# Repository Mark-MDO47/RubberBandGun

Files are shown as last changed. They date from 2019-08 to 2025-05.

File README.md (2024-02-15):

# RubberBandGun
A high-tech SciFi imagining of the rubber band gun.

Both working prototypes were shown at the Asheville Maker Faire on May 07, 2022 in Asheville, N.C. Estimates are that 100 people fired rubber bands out of the RBG!<br>
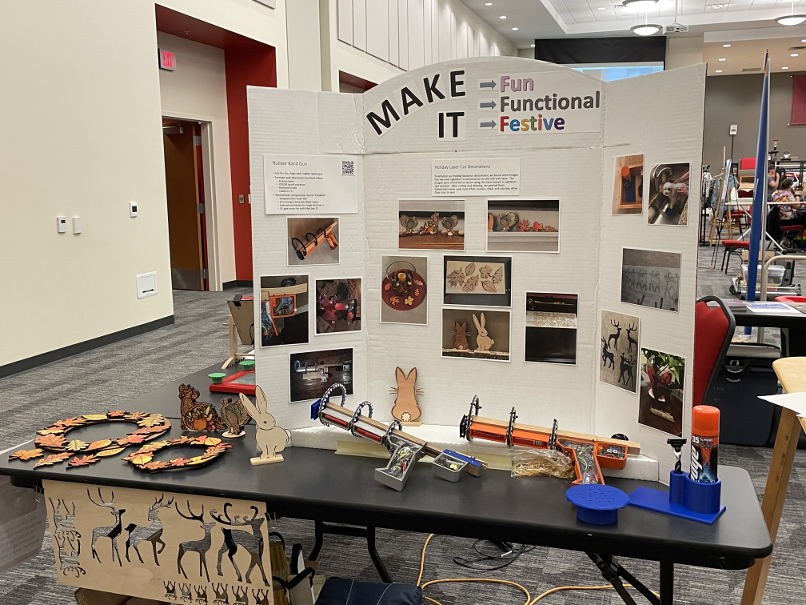
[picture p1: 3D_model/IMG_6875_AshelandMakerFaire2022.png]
Both Rubber Band Guns at Asheville Maker Faire on May 2022


**Table Of Contents**
* [Top](#rubberbandgun "Top")
* [Videos](#videos "Videos")
* [Images](#images "Images")
* [Introduction](#introduction "Introduction")
* [Parts List](#parts-list "Parts List")
  * [Release Mechanism Software Dependency](#release-mechanism-software-dependency "Release Mechanism Software Dependency")
* [Sounds](#sounds "Sounds")
  * [Sound Effects](#sound-effects "Sound Effects")
  * [Voice Audio](#voice-audio "Voice Audio")
* [LED Patterns](#led-patterns "LED Patterns")
* [Extras](#extras "Extras")
* [Guide to README and Other Docs](#guide-to-readme-and-other-docs "Guide to README and Other Docs")

## Videos
[Top](#rubberbandgun "Top")<br>
Here is a new (2023-07-14) video showing the completed orange "Sidewinder" rubber band gun with a fairly complete showing of its features.
* https://youtu.be/TYfbrVR2EE8

Here is a video showing the completed orange "Sidewinder" rubber band gun at night:
* https://youtu.be/M4FHvP624Kg

Here is a 2020-09-25 video demonstrating most of the software running on a prototype:
* https://youtu.be/njpYX-5Zv9Y

## Images
[Top](#rubberbandgun "Top")<br>

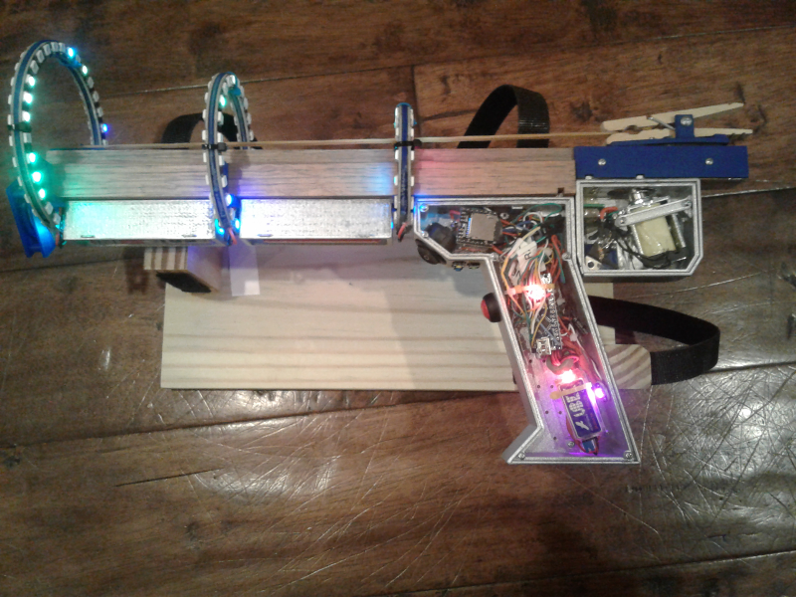
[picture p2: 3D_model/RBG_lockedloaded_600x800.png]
Top View of Jim's assembled SINGLETON SILVER RBG with solenoid and sliding barrel

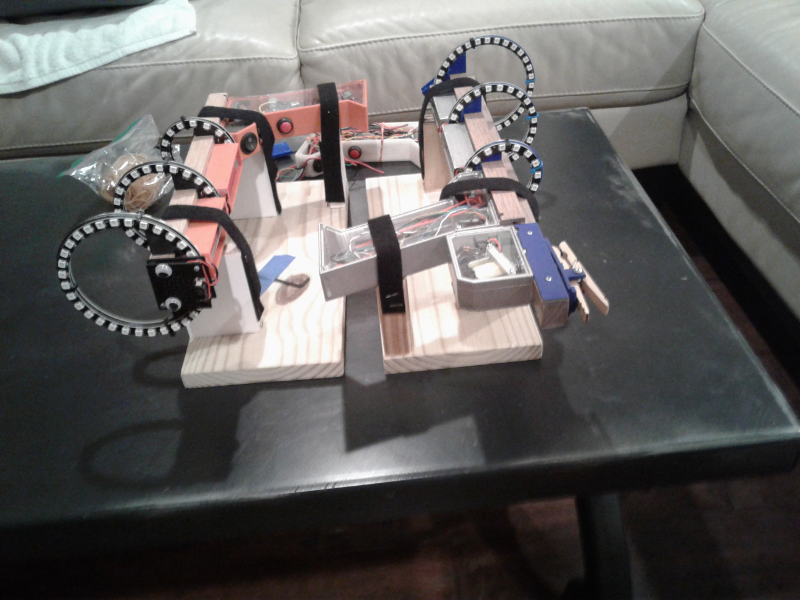
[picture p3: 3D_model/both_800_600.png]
Both RBGs side by side

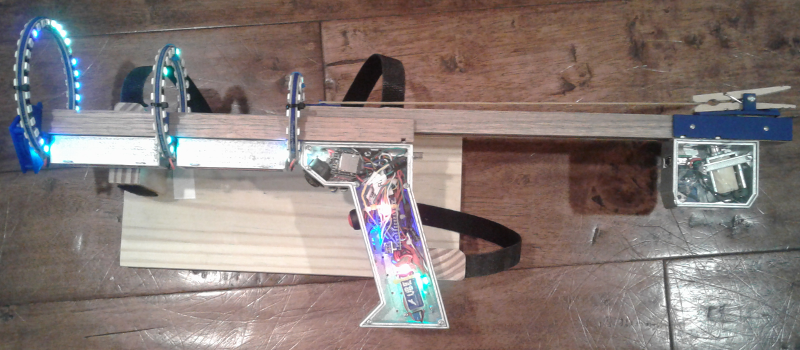
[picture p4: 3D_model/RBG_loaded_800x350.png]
Loading a rubber band in Jim's assembled SINGLETON SILVER RBG with solenoid and sliding barrel

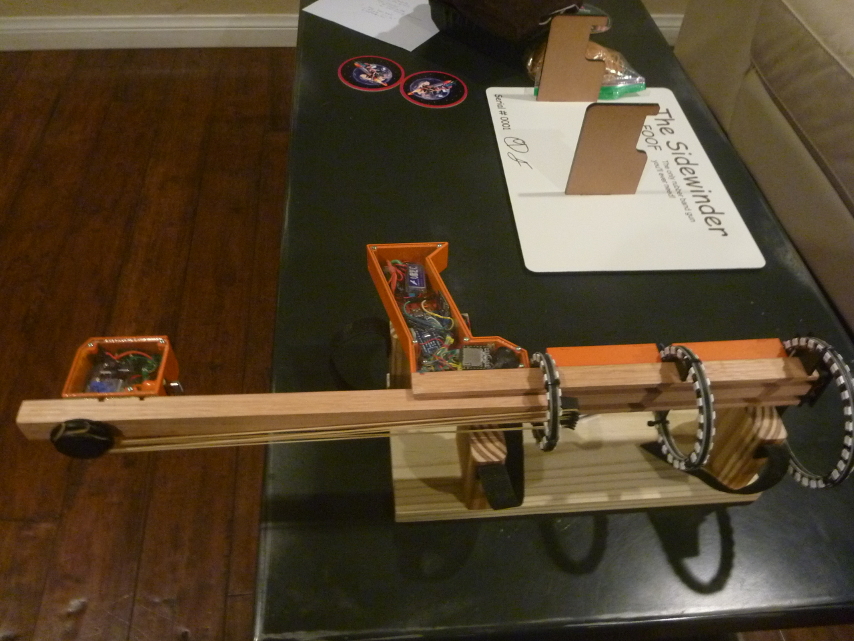
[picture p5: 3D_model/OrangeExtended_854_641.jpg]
Extended view of ORANGE SIDEWINDER Science Fiction Rubber Band Gun with Motor attachment

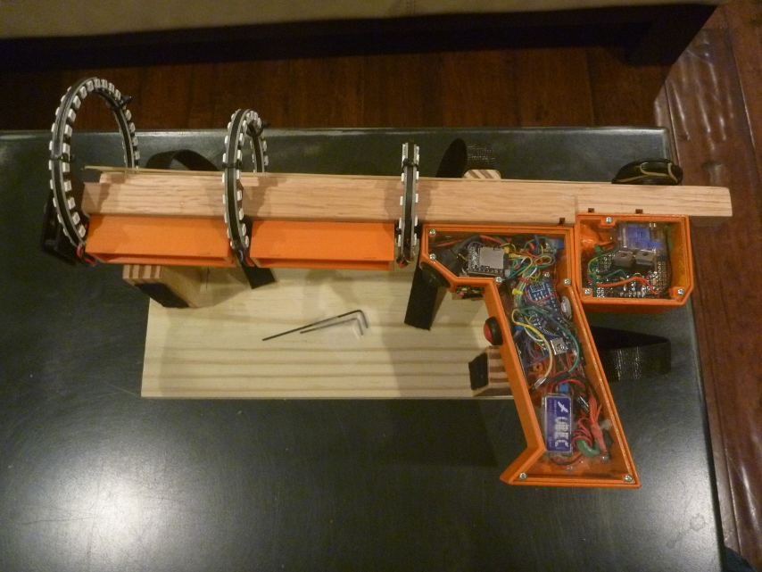
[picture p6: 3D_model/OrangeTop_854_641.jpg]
Top view of ORANGE SIDEWINDER Science Fiction Rubber Band Gun with Motor attachment

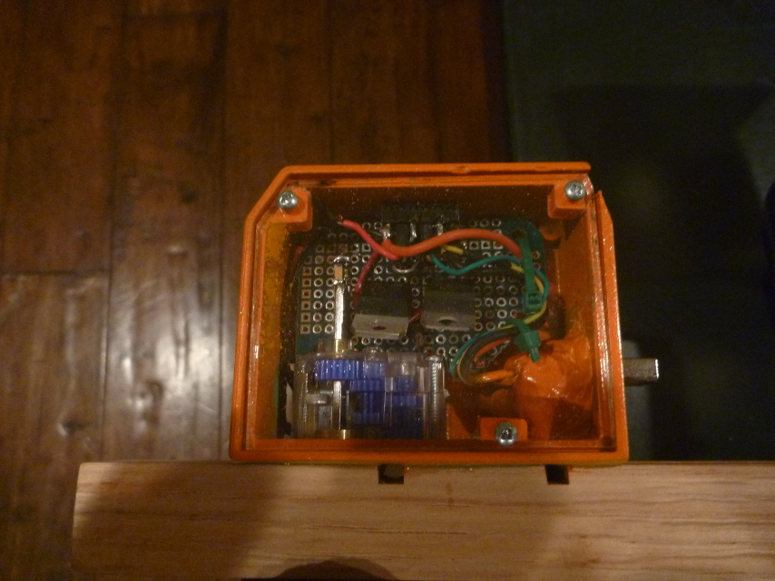
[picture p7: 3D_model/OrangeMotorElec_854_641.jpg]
View of ORANGE SIDEWINDER Science Fiction Rubber Band Gun Motor electronics

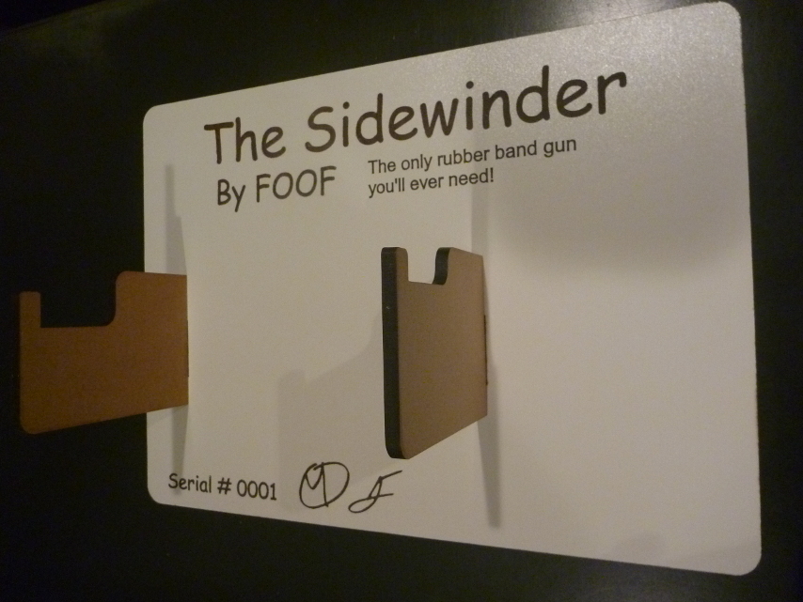
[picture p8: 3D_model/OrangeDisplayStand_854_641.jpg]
View of Display Stand for ORANGE SIDEWINDER Science Fiction Rubber Band Gun


## Introduction
[Top](#rubberbandgun "Top")<br>
Jim and I made a Science-Fiction Rubber Band Gun!

It has three rings of WS2812b 5050 RGB LED Ring proceeding up the barrel, each one larger than the previous in a "blunderbuss" shape. Note: this shape when applied to a handgun was known as a dragon, from which the term dragoon; see https://en.m.wikipedia.org/wiki/Blunderbuss

When fired, it plays a chosen sound. This could be a sequence similar to a "soundified" rendition of two neutron stars colliding
* https://www.gw-openscience.org/audiogwtc1 - search for GW170817

See the [Sounds](#sounds "Sounds") section below and the sounds README for more info.
* https://github.com/Mark-MDO47/RubberBandGun/blob/master/sounds/README.md

At the same time as the sound, the LED rings do patterns to make it look like they are being charged up followed by a sequential pulsing that would convince anyone who knows absolutely less than nothing about such things that a rail-gun effect is propelling the rubber band down the central tube. These rings are composed of WS2812B individually addressable color LEDs controlled by the fantastic FastLED library. See the [LED Patterns](#led-patterns "LED Patterns") section below and the PartsInfo README for more info.
* https://github.com/Mark-MDO47/RubberBandGun/blob/master/PartsInfo/README.md

And the RBG is a talking Rubber Band Gun! It can use its own built-in speaker or connect to a Bluetooth speaker, it has voice menus to allow configuration of sounds and LED effects. The video at https://youtu.be/njpYX-5Zv9Y goes through some of the menus using a Bluetooth speaker.

## Parts List
[Top](#rubberbandgun "Top")<br>
We have two working prototypes using these parts. The prices and parts availability have not been updated recently.
* https://github.com/Mark-MDO47/RubberBandGun/blob/master/PartsList.md

The barrel of the Rubber Band Gun is made from wood, with a sliding barrel attachment to assist in stringing the rubber band through the LED rings. The rest including the handgrip is 3-D printed.

### Release Mechanism Software Dependency
[Top](#rubberbandgun "Top")<br>
The "SILVER" SINGLETON RBG uses the solenoid release mechanism through the CLOTHESPIN to fire the rubber band.

Jim felt like this wasn't reliable enough and designed a SIDEWINDER mechanism that uses a motor to release one or more rubber bands at a time; this was used on the "ORANGE" RBG.

The current parts list and schematics contain both the CLOTHESPIN (SOLENOID) and the SIDEWINDER (MOTOR) mechanisms.

Git tag Silver-1.0 is the version of software that is in the SILVER CLOTHESPIN (SOLENOID) RBG
* There is a definition of DLYSOLENOID in RBG_SciFi_StatesAndInputs.h that needs to be adjusted if using the SIDEWINDER (MOTOR). See the comments near that definition if interested.

Development is continuing to make a minimum as well as a maximum activation time for the solenoid or motor mechanism. This will get a tag when complete and tested. SOLENOID_IF_NONZERO chooses CLOTHESPIN versus SIDEWINDER operation and sets the values of DLYSOLENOID_MIN and DLYSOLENOID_MAX.
* Define SOLENOID_IF_NONZERO as 1 for CLOTHESPIN (SOLENOID) processing.
  * The Silver-1.0 version DLYSOLENOID corresponds to DLYSOLENOID_MAX in the later versions.
* Define SOLENOID_IF_NONZERO as 0 for SIDEWINDER (MOTOR) processing; this also activates the ability to control the motor time with the trigger button between DLYSOLENOID_MIN and DLYSOLENOID_MAX. I had initially added some other factors like when the shooting sound ended, but opted for more predictable behavior.
  *  When it shoots, it will do a minimum of 1/4 turn and basically keep turning until you let the trigger off or it reaches 1 complete turn. This allows me to put a rubber band on every other notch and just get a single shot by momentary trigger press or multiple shots by holding the trigger down until done.

## Sounds
[Top](#rubberbandgun "Top")<br>
All sounds for the RBG were processed by Audacity, which can be found at https://www.audacityteam.org/

Voice sounds were generated by the eSpeak text-to-speech program version 1.48.04. The original code can be found at http://espeak.sourceforge.net/ while current development is at https://github.com/espeak-ng/espeak-ng
* Postprocessing was done by Audacity

The sounds reside on a 16Gbyte SD card inserted in the YX5200 audio module. Also on that SD card is an ATTRIBUTION directory containing an HTML file with attributions for the sounds used in this project.

Note that the sounds were de-stereo'd, chopped up, and in many cases modified and/or combined with other sounds. There is not a one-to-one onto relationship between the source of the sounds and the sounds as played by the Rubber Band Gun.

* As for many aspects of the RGB, the text-to-speech is semi-automated with StateTable_minimal.xlsx used to control generation and to associate sounds with RBG events.
* See https://github.com/Mark-MDO47/RubberBandGun/blob/master/sounds/README.md

### Sound Effects
[Top](#rubberbandgun "Top")<br>
See the Readme.md in https://github.com/Mark-MDO47/RubberBandGun/tree/master/sounds for attribution and other information about the sounds that are used in this project.

See https://github.com/Mark-MDO47/RubberBandGun/blob/master/RBG_arduino/README.md for how sounds are integrated into the Arduino code.

### Voice Audio
[Top](#rubberbandgun "Top")<br>
A few of the voices are recordings of members of my family or of me. The remainder are generated by the eSpeak text to speech program and post-processed by Audacity.

## LED Patterns
[Top](#rubberbandgun "Top")<br>
FastLED is the library I use for controlling these color addressable LEDs

* https://www.arduino.cc/reference/en/libraries/fastled/
* https://github.com/FastLED/FastLED

If you are new to FastLED, look at this famous demo code to see how easy it can be

* https://github.com/FastLED/FastLED/blob/master/examples/DemoReel100/DemoReel100.ino

See https://github.com/Mark-MDO47/RubberBandGun/blob/master/RBG_arduino/README.md for how LED Patterns are integrated into the Arduino code.
* As for many aspects of the RGB, the LED Patterns are semi-automated with StateTable_minimal.xlsx to associate LED Patterns with RBG events.

## Extras
[Top](#rubberbandgun "Top")<br>
The basic information from the references below is also on this repository, but the repositories below are more standalone and better for using on your own projects.

Get tips and some code for using the YX5200 Audio module: https://github.com/Mark-MDO47/AudioPlayer-YX5200

Get tips and some code for programming the KCX_BT_EMITTER Bluetooth Audio Transmitter module: https://github.com/Mark-MDO47/BluetoothAudioTransmitter_KCX_BT_EMITTER
Be aware that the KCX_BT_EMITTER module expects 5V power and 5V serial interface signals; I have heard of people who found that the ESP32 did not work when directly used as the Programming Arduino. This can be easily accommodated by using a true Arduino version or a cheap clone Arduino Uno or Arduino Nano classic.

## Guide to README and Other Docs
[Top](#rubberbandgun "Top")<br>
Here are the README docs available on this repository:
* [This README File](https://github.com/Mark-MDO47/RubberBandGun/blob/master/README.md "This README File")
* [Parts List](https://github.com/Mark-MDO47/RubberBandGun/blob/master/PartsList.md "Parts List")
* [Arduino Code Description](https://github.com/Mark-MDO47/RubberBandGun/blob/master/RBG_arduino/README.md "Arduino Code Description")
* [Parts Info Overview](https://github.com/Mark-MDO47/RubberBandGun/blob/master/PartsInfo/README.md "Parts Info Overview")
* [YX5200 Audio Module Info](https://github.com/Mark-MDO47/RubberBandGun/blob/master/PartsInfo/YX5200.md "YX5200 Audio Module Info")
* [Sound Sources and Attribution](https://github.com/Mark-MDO47/RubberBandGun/blob/master/sounds/README.md "Sound Sources and Attribution")
* [KiCad files for Schematic-Style Rubber Band Gun Wiring PDF](https://github.com/Mark-MDO47/RubberBandGun/tree/master/KiCad "KiCad files for Schematic-Style Rubber Band Gun Wiring PDF")
* [Autocad Fusion 360 files for 3D Printed Parts](https://github.com/Mark-MDO47/RubberBandGun/blob/master/3D_model/ReadME.md "Autocad Fusion 360 files for 3D Printed Parts")

Here are some other docs available on this repository:
* [Schematic-Style Rubber Band Gun Wiring PDF](https://github.com/Mark-MDO47/RubberBandGun/blob/master/RubberBandGun_Wiring.pdf "Schematic-Style Rubber Band Gun Wiring PDF")
* [Overview of Building the Rubber Band Gun Software](https://github.com/Mark-MDO47/RubberBandGun/blob/master/BuildRubberBandGunSoftware.pdf "Overview of Building the Rubber Band Gun Software")
* [How To Program the KCX-BT-EMITTER BlueTooth Module](https://github.com/Mark-MDO47/RubberBandGun/blob/master/ProgrammingArduino_SerialMonitor_SampleOutput.pdf "How To Program the KCX-BT-EMITTER BlueTooth Module")
* [Wiring Tips when Building the FOOF RBG](https://github.com/Mark-MDO47/RubberBandGun/blob/master/FOOF_RBG_Wiring.pdf "Wiring Tips when Building the FOOF RBG")

Here are some other useful docs etc. available on other repositories:
* [Details of Microchip Technology ATMega Processors including 328P used in Arduino Nano](http://ww1.microchip.com/downloads/en/DeviceDoc/ATmega48A-PA-88A-PA-168A-PA-328-P-DS-DS40002061A.pdf "Details of Microchip Technology ATMega Processors including 328P used in Arduino Nano")
* [Best Detailed YX5200 Audio Module DataSheet I Could Find](https://github.com/PowerBroker2/DFPlayerMini_Fast/blob/master/extras/FN-M16P%2BEmbedded%2BMP3%2BAudio%2BModule%2BDatasheet.pdf "Best Detailed YX5200 Audio Module DataSheet I Could Find")
* [AT Commands for KCX-BT-EMITTER Bluetooth Audio Module (use Google Translate)](https://item.taobao.com/item.htm?spm=a21wu.12321156-tw.0.0.7e76d1c7xEOcFZ&id=570274835710 "AT Commands for KCX-BT-EMITTER Bluetooth Audio Module (use Google Translate)")
* [Electro-Tech-Online.com Forum Discussion on AT Commands for KCX-BT-EMITTER](https://www.electro-tech-online.com/threads/kcx_bt_emitter-low-cost-bluetooth-bt-audio-module.158156/ "Electro-Tech-Online.com Forum Discussion on AT Commands for KCX-BT-EMITTER")
* [Details of WorldSemi WS2812B LED Operation](https://cdn-shop.adafruit.com/datasheets/WS2812B.pdf "Details of WorldSemi WS2812B LED Operation")
* [Solenoid Driver Circuit from Adafruit](https://cdn-shop.adafruit.com/product-files/412/solenoid_driver.pdf "Solenoid Driver Circuit")

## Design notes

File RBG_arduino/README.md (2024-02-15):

# Arduino Code for the Rubber Band Gun (RBG): RBG_SciFi.ino
The Arduino and its sketch RBG_SciFi.ino handily manage all the tasks including voice menus, storage of user configuration, LED rings, and sound generation. It can do this because RBG_SciFi.ino has pre-computed tables built in that guide it, especially for state transitions and special effects.

**Table Of Contents**
* [Top](#arduino-code-for-the-rubber-band-gun-(rbg)-rbg_scifiino "Top")
* [Generating Tables for the Code](#generating-tables-for-the-code "Generating Tables for the Code")
* [RBG_SciFi_StatesAndInputs.h](#rbg_scifi_statesandinputsh "RBG_SciFi_StatesAndInputs.h")
  * [RBG_SciFi_StatesAndInputs.h - Effect Types and Ranges](#rbg_scifi_statesandinputsh-\--effect-types-and-ranges "RBG_SciFi_StatesAndInputs.h - Effect Types and Ranges")
  * [RBG_SciFi_StatesAndInputs.h - Factory Reset Configurations](#rbg_scifi_statesandinputsh-\--factory-reset-configurations "RBG_SciFi_StatesAndInputs.h - Factory Reset Configurations")
* [Libraries and Capabilities Used](#libraries-and-capabilities-used "Libraries and Capabilities Used")
* [The Code Itself](#the-code-itself "The Code Itself")
    * [Special Code Topic: LED Patterns](#special-code-topic-led-patterns "Special Code Topic: LED Patterns")
* [Reprogramming in the Completed Rubber Band Gun](#reprogramming-in-the-completed-rubber-band-gun "Reprogramming in the Completed Rubber Band Gun")
  * [RBG_SciFi.ino](#rbg_scifiino "RBG_SciFi.ino")
  * [Sounds](#sounds "Sounds")
  * [Separate Programming Arduino for Bluetooth Module](#separate-programming-arduino-for-bluetooth-module "Separate Programming Arduino for Bluetooth Module")

## Generating Tables for the Code
See the following for an overview of generating the tables for the RBG_SciFi.ino code:
* https://github.com/Mark-MDO47/RubberBandGun/blob/master/BuildRubberBandGunSoftware.pdf

The file **StateTable_minimal.xlsx** is the heart of RBG_SciFi.ino. It has multiple tabs that are used to generate the code for the RBG.
* **StateTable:** the main tab, used in generating the myStateTable struct and associated #define's. This is done by running makeStateTable.py. This tab controls the overall action of the RBG.
* **RULES:** a list of things to keep in mind when changing the StateTable tab. Sorry, not a tutorial, just notes.
* **debugging:** where I capture serial port debugging info to diagnose why my stupid code doesn't do what I want and not what I say.
  * There is a list of "grep" commands used to filter this down; then I load the mdo2.txt into a spreadsheet in column B, put the Excel formula after the grep's in A1, and copy down the length. I then sort and remove duplicates. This uses my tiny mdoUniq.py routine to get rid of lines that are duplicate between a start and end string.
* **YX5200 info:** a bunch of info from other sources referenced in the parts directory. Could delete this tab now but it took me a while to make things work reliably.
* ***WAVformat:*** some info about the WAV file header format; used to check WAV file parameters to make sure they were all compatible with the YX5200
* **Sounds:** this includes the text for use in text-to-speech synthesis for the robotic sounds. This is generated by running RobotSounds.py. The sound numbers are used in the StateTable tab. This is described more in https://github.com/Mark-MDO47/RubberBandGun/blob/master/PartsInfo/YX5200.md.
* **LEDpatterns:** this helps me organize the LED patterns by number and generate lookupLEDpatternTbl. There is a short description in this tab of the use of the fabulous FastLED library and the generation and organization of the LED patterns.
* **FactorySettings:** This tab defines the Factory Settings for sounds and LED patterns to be used for all of the effects (such as shooting a rubber band mEFCT_SHOOT, "lock and load" reconnect of a loaded rubber band mEFCT_LOCK_LOAD, etc.)

## RBG_SciFi_StatesAndInputs.h
If StateTable_minimal.xlsx is the heart of RBG_SciFi.ino, then... OK, I won't continue down that path.

### RBG_SciFi_StatesAndInputs.h - Effect Types and Ranges
Search for **mEFCT_** until you find mEFCT_WIND_UP and you will see a list of effect types in groups of 10. There are up to 9 (sorry, I wasted one for convenience) LED and Sound effects for each one of these effect groups. cfgMaxSoundForType and cfgMaxLEDForType show the end range for these effects per type. The effect type max ranges are: 001 to 009 - wind-up effects; 011 to 019 - shoot effects; 021 to 029 - open barrel effects; 031 to 039 - lock and load barrel effects; 041 to 049 - initial power-up effects; 051 to 059 - waiting for trigger. The last one is different: 061 to 127 - unique effects used to navigate menus or other activities.
* the PROGMEM stores four Factory Settings for all the sounds and LED effects; each sound/LED combination is for a single effect (such as mEFCT_SHOOT) when active in a particular Factory Setting (0 through 3)
* EEPROM has a space for a copy of all four settings; the EEPROM version is configurable via audio menus.
* At startup, if the checksum in EEPROM storage doesn't match the data in EEPROM, the four PROGMEM Factory Settings are copied into EEPROM. This is equivalent to a complete "Factory Reset" from the audio menus.
* While running, the RBG cycles through the configurations automatically each time a rubber band is shot (activities effect).
* The configuration at position 0 is the "running setting" position used for editing via audio menus; it can be copied back and forth to other positions via audio menus.
* For each of the configurable settings, there is a number in that range stored in EEPROM for both LED and Sound effects for each of the effect groups (except for the unique effects such as audio menu items). These are changeable via voice menu as seen in the "Operations" chart in https://github.com/Mark-MDO47/RubberBandGun/blob/master/BuildRubberBandGunSoftware.pdf. To change one of the settings for one of the configurations, make that configuration the current configuration then choose the path **Config**, **Sound or LED**, and **When, What, Choose**. The "When" refers to one of the ranges, for instance "wind-up effects". The "What" refers to either the **Sound** effect or the **LED** effect. After that you choose among the effects through the range stored in cfgMaxSoundForType or cfgMaxLEDForType as appropriate.

### RBG_SciFi_StatesAndInputs.h - Factory Reset Configurations
Search for factory_effect_configs and you will find the table with the Factory Reset configurations for Sound and LED patterns for all four configurable settings. These are organized with 32 bytes per configurable setting, both for convenience and for expansion. 16 bytes are for Sound effects and 16 bytes are for LED effects. The first 6 of these 16-byte regions are used for the Effect Types we discussed above. The number stored is in the range [1-9], the effect type is implicit in the position of the byte.
* Factory Reset via the audio menus will set one or all four of these configurations back to the PROGMEM default.
* If you do lots of configuration changes to the RBG and then just want to go back to the factory reset configuration, follow the "Operations" chart in https://github.com/Mark-MDO47/RubberBandGun/blob/master/BuildRubberBandGunSoftware.pdf and choose the path **Config**, **Cfg Reset Copy**, and **Fctry Rst Copy**. The option to choose for complete reset of all the effect settings would be: "Erase the running setting and erase all saved auxilliary settings and reset to the factory settings".
* The other option would be to restore only the running setting: "Erase the running setting only and reset the running setting to the factory settings."

## Libraries and Capabilities Used
Once all those tables and #defines are generated and installed in the Arduino code, we still have the rest of the code.

Major libraries used are mostly described in the following:
* https://github.com/Mark-MDO47/RubberBandGun/blob/master/PartsInfo/README.md

One other important general thing I use is PROGMEM and associated F() macro to store constants (strings and various numbers) in program storage instead of RAM. Here are a couple of useful articles about this capability:
* http://www.gammon.com.au/progmem
* https://www.arduino.cc/reference/en/language/variables/utilities/progmem/

## The Code Itself
I won't go into too much detail here, but this is a bit of a roadmap to **RBG_SciFi.ino**.
* **getButtonInput()** retrieves a bit mask for all the buttons and a few other states like end-of-sound and lock-and-load-status
* **RBG_processStateTable()** is used to go through the state table in the myStateTable struct
  * it may call **RBG_startEffectLED()** and/or **RBG_startEffectSound()**
* **RBG_waitForInput()** is where we wait for results of getButtonInput() to match something that would cause a state transition; also some logic for what we would do in certain circumstances.
* **doPattern()** is used to continue an LED time-sequence pattern. Sounds continue by themselves to completion, so no such routine for sounds
* **eeprom_check_init()** is used to verify we have a valid EEPROM configuration and if not to load the factory configuration
* **RBG_specialProcShoot()** and **RBG_specialProcStopShoot()** - used to turn on and off the solenoid/motor depending if it is the CLOTHESPIN/SILVER or the SIDEWINDER/ORANGE RBG. After experimentation with the SIDEWINDER, I am leaning towards having part of the equation for when to StopShoot being when the trigger is released. Still experimenting, but it would give the ability to load 3 rubber bands and single-shoot them.

#### Special Code Topic: LED Patterns
I thought this could use some more explanation.

FastLED is the library I use for controlling these WS2812B color addressable LEDs:
* https://www.arduino.cc/reference/en/libraries/fastled/
* https://github.com/FastLED/FastLED

If you are new to FastLED, look at this famous demo code to see how easy it can be
* https://github.com/FastLED/FastLED/blob/master/examples/DemoReel100/DemoReel100.ino

In the RBG I use four unmodified routines from DemoReel100. These routines take no parameters.
* **bpm()**
* **confetti()**
* **juggle()**
* **rainbowWithGlitter()**

I also use three modified routines from DemoReel100. The first routine takes no parameters, but the other two take a parameter.
* **RBG_bpm_rings()**
* **RBG_confetti_fadeby()**
* **RBG_juggle_numdot_ring()**

I also use two routines of my own invention; these routines take parameter(s).
* **RBG_diskDownTheDrainOrRotate()**
* **RBG_RailGunEffect()**

The LED patterns can string these routines together to make one composite pattern.

FYI diskDownTheDrainOrRotate() was originally written for the Graduation Cap project https://github.com/Mark-MDO47/GraduationCap2017. Some modifications were made for use in the RBG.

## Reprogramming in the Completed Rubber Band Gun

### RBG_SciFi.ino
Take the clear acrylic cover off, **pull back the barrel/solenoid/motor assembly** as if loading, turn the RBG power on, plug in the Arduino NANO USB connector to your computer, and program. Reverse to disconnect.

NOTE: when the RBG power is on while the USB connector is connected and periodically resetting the Arduino, it continuously resets and pulses the solenoid/motor circuit at an interval of about 1.5 seconds. This might eventually damage the solenoid/motor or its circuitry, so it is important to pull back the barrel/solenoid/motor assembly before powering on.

NOTE: The reason I suggest powering on the RBG while programming is so that the entire RBG is not being powered through our inexpensive clone Arduino Nano.

### Sounds
Take the clear acrylic cover off, turn the RBG power off, hold the YX5200 on the far end while pushing the SD card in and releasing. The SD card should pop out partway; remove it. Connect the SD card to your PC (typically using a USB adaptor) and use the instructions for copyem.py described in https://github.com/Mark-MDO47/RubberBandGun/blob/master/PartsInfo/YX5200.md. Eject the SD card from your PC, hold the YX5200 on the far end while pushing the SD card back in until it clicks. The SD card should stay almost all the way in. Put the clear acrylic cover back on.

### Separate Programming Arduino for Bluetooth Module
There is an Arduino routine **ProgrammingArduino.ino** run on a physically separate external Arduino (not part of the RBG) to program the KCX_BT_EMITTER module to recognize your bluetooth speaker or headphones and not just connect to the first one it sees. You can read about this process here:
* https://github.com/Mark-MDO47/RubberBandGun/blob/master/ProgrammingArduino_SerialMonitor_SampleOutput.pdf

Why a physically separate Arduino? We used so many output pins on the Arduino in the RBG that there were not enough unused pins to do this job. Also, attempting to do this function using voice menus would be tedious.

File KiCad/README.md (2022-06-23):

# KiCad files
The file to open in KiCad is RubberBandGun.pro

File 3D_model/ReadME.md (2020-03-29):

Jim is doing the 3-D Modeling using a personal version of Autocad Fusion 360. The following URLs allow you to view and/or download the files in their current state.

- RBG body: https://eur05.safelinks.protection.outlook.com/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
- clothespin holder: https://eur05.safelinks.protection.outlook.com/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
- single battery holder: https://eur05.safelinks.protection.outlook.com/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
- small LED ring attachment: https://eur05.safelinks.protection.outlook.com/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
- medium LED ring attachment: https://eur05.safelinks.protection.outlook.com/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
- large LED ring attachment: https://eur05.safelinks.protection.outlook.com/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

Still to come: solenoid body, speaker mount

I must admit that the web viewer for Autocad Fusion 360 is quite excellent!

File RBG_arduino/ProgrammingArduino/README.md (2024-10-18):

This is used in an Arduino to program a Bluetooth MAC address into the YX5200 module.

Currently the programming on the Orange Sidewinder RBG is<br>
```
--CMD 2 AT+VMLINK?
OK+VMLINK
BT_ADD_NUM=2
BT_NAME_NUM=2
Last_Add=0x1adad504eaed
VM_MacAdd0=0x1adad504eaed
VM_MacAdd1=0xf44efdecd39d
VM_Name0=E-go III Orange
VM_Name1=S1 Pro RBG Orange
```

| Order | Name | Mac Address |
| --- | --- | --- |
| 1 | E-go III Orange | 0x1adad504eaed |
| 2 | S1 Pro RBG Orange | 0xf44efdecd39d |

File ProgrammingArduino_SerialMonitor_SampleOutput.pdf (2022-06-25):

# Using the Programming Arduino, Author: Mark Olson

## https://github.com/Mark-MDO47/RubberBandGun

## https://github.com/Mark-

MDO47/RubberBandGun/blob/master/RBG_arduino/ProgrammingArduino/ProgrammingArduino.ino (https://github.com/Mark-MDO47/RubberBandGun/blob/master/RBG_arduino/ProgrammingArduino/ProgrammingArduino.ino)

We use the Programming Arduino to program the VMLINK table in the KCX_BT_EMITTER Bluetooth Audio Transmitter Module for the Rubber Band Gun (RBG). VMLINK is the table that stores the info on Bluetooth speakers that the KCX_BT_EMITTER would automatically connect to. This KCX_BT_EMITTER VMLINK table can store info about more than one Bluetooth receiver (speaker, headphone, etc.) device. If info about more than one Bluetooth receiver is stored in VMLINK, the KCX_BT_EMITTER would try to connect to the first entry that was a device that it could see on its scan of Bluetooth devices.

# Connections

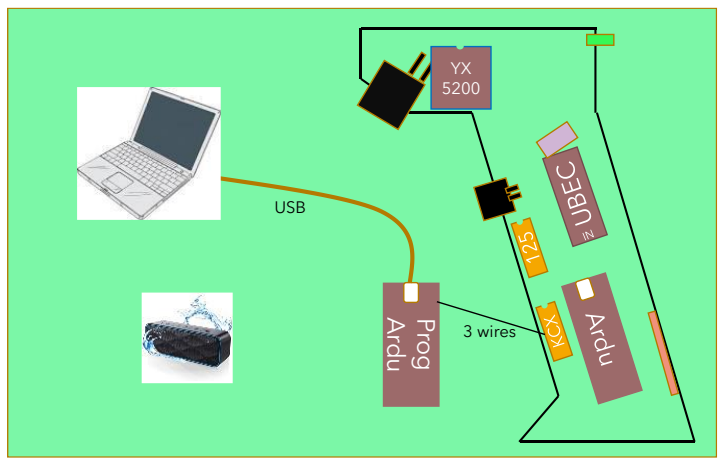
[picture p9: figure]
Ardu; Prog; 3 wires; USB

# Connect the Programming Arduino

## 1. On Rubber Band Gun (RBG) - Power off RBG - Remove the clear cover on the handle of the RBG - Inside the handle, find the female jumper connectors for the KCX_BT_EMITTER chip (near front of handle)

- | label | color of wire
- | GND | BLACK
- | 2 RX | GREEN
- | 9 TX | YELLOW

## 2. On separate programming Arduino (using +5V interfaces) - Power off programming Arduino by disconnecting from USB - Connect jumper wires with male ends as follows - Pin color of wire

- | GND | BLACK
- | D2 RX | GREEN (Arduino TX)
- | D9 TX | YELLOW (Arduino RX)

3. Connect the programming Arduino jumper wires to the RBG jumper wires using color as the guide.

# Disconnect the Programming Arduino

1. Ensure that programming Arduino is disconnected from USB for PC running the Arduino software; pull back the barrel/solenoid/motor assembly as if loading 2. On Rubber Band Gun (RBG) - Power off RBG 3. On separate programming Arduino (using +5V interfaces) - Disconnect the programming Arduino jumper wires from the RBG jumper wires 4. On Rubber Band Gun (RBG)
- Store the jumper connectors safely in the handle and attach the clear cover on the handle of

## the RBG

# Programming

1. Connect the Programming Arduino (see above) 2. On Rubber Band Gun (RBG) - Power on RBG 3. On the separate programming Arduino (using +5V interfaces) - Connect programming Arduino to USB for PC running the Arduino software - Upload the sketch from ProgrammingArduino.ino into the programming Arduino - Open Serial Monitor by selecting menu "Tools" -> "Serial Monitor" 4. Follow instructions on the serial monitor - After each selected step, wait for the string "--- KCX_BT_EMITTER PROGRAMMING STEP COMPLETE ---" 5. Disconnect programming Arduino from USB for PC running the Arduino software 6. Disconnect the Programming Arduino (see below)

# Sample Session

For this session, we start with the “Old and Broken” device in the VMLINK table. We want to remove that and put in our “S1 Pro” device. Because both Jim and Mark have S1 Pro Bluetooth speakers, I will label this one “S1 Pro MDO” (you do not need to use the default name provided by the manufacturer).

In order to add S1 Pro MDO we need to know what its unique address is. This can be found by turning the speaker on and telling the KCX_BT_EMITTER to scan for Bluetooth speakers and headphones that it can connect to.

The table below shows the Serial Monitor output from a session of programming the KCX_BT_EMITTER

## Bluetooth Audio Transmitter module. The colors for the serial monitor output column are:

- BLACK - communication from the Programming Arduino, either asking for directions or

giving feedback. It often asks which “programming step” to execute: SCAN, DISPLAY, ADD, or DELETE ALL.

- RED - “AT” commands sent to the KCX_BT_EMMITER. It takes several “AT” commands to perform

a user-selected “programming step”.

- GREEN - KCX_BT_EMMITER direct status response to the “AT” command.
- BLUE - communication from the KCX_BT_EMMITER reporting what it sees on its scan.

Programming Arduino Serial Monitor output | Comments
Bluetooth Programming Arduino init... completed! 1 - Scan for Bluetooth receiver devices (such as speaker, headphones, etc.) 2 - Display stored auto-connect Bluetooth receiver devices 3 - Add one auto-connect Bluetooth receiver device to storage 4 - Delete all auto-connect Bluetooth receiver devices from storage ==> | Startup Request user to command action User types in number
1=SCAN | feedback to user on selection
ALL Devices=0 | Scan output from KCX_BT_EMITTER
--CMD 0 AT+ | “Aliveness” command
OK+ | command response
New Devices:1,MacAdd:0xf44efdecd39d,Name:S1 Pro ALL Devices=1 MacAddr=0xf44efdecd39d,Name=S1 Pro | Scan output
--CMD 1 AT+REST | RESET cmd to KCX_BT_EMITTER
OK+REST | command response
POWER ON | command response
New Devices:1,MacAdd:0xf44efdecd39d,Name:S1 Pro ALL Devices=1 MacAddr=0xf44efdecd39d,Name=S1 Pro | Scan output
--CMD 2 AT+SCAN | SCAN cmd to KCX_BT_EMITTER
OK+SCAN
New Devices:1,MacAdd:0xf44efdecd39d,Name:S1 Pro ALL Devices=1 MacAddr=0xf44efdecd39d,Name=S1 Pro New Devices:1,MacAdd:0xf44efdecd39d,Name:S1 Pro ALL Devices=1 MacAddr=0xf44efdecd39d,Name=S1 Pro New Devices:1,MacAdd:0xf44efdecd39d,Name:S1 Pro | Scan output

--- KCX_BT_EMITTER PROGRAMMING STEP COMPLETE ---1 - Scan for Bluetooth receiver devices (such as speaker, headphones, etc.) 2 - Display stored auto-connect Bluetooth receiver devices 3 - Add one auto-connect Bluetooth receiver device to storage 4 - Delete all auto-connect Bluetooth receiver devices from storage ==>

2=DISPLAY

--CMD 0 AT+
OK+
ALL Devices=1 MacAddr=0xf44efdecd39d,Name=S1 Pro New Devices:1,MacAdd:0xf44efdecd39d,Name:S1 Pro ALL Devices=1 MacAddr=0xf44efdecd39d,Name=S1 Pro

Programming Arduino Serial Monitor output | Comments

--CMD 1 AT+REST
OK+REST
POWER ON
New Devices:1,MacAdd:0xf44efdecd39d,Name:S1 Pro ALL Devices=1
MacAddr=0xf44efdecd39d,Name=S1 Pro
--CMD 2 AT+VMLINK? | Show the VMLINK info cmd
OK+VMLINK BT_ADD_NUM=1 BT_NAME_NUM=1 Last_Add=0x00000000000 VM_MacAdd0=0x00000000012 VM_Name0=Old and Broken | Old and Broken device is in the VMLINK table, but we want to remove that and put in our S1 Pro device

New Devices:1,MacAdd:0xf44efdecd39d,Name:S1 Pro ALL Devices=1 MacAddr=0xf44efdecd39d,Name=S1 Pro

--- KCX_BT_EMITTER PROGRAMMING STEP COMPLETE ---1 - Scan for Bluetooth receiver devices (such as speaker, headphones, etc.) 2 - Display stored auto-connect Bluetooth receiver devices 3 - Add one auto-connect Bluetooth receiver device to storage 4 - Delete all auto-connect Bluetooth receiver devices from storage ==>

4=DELETE ALL
New Devices:1,MacAdd:0xf44efdecd39d,Name:S1 Pro ALL Devices=1

--CMD 0 AT+
OK+
ALL Devices=1 MacAddr=0xf44efdecd39d,Name=S1 Pro New Devices:1,MacAdd:0xf44efdecd39d,Name:S1 Pro
--CMD 1 AT+REST | RESET command
OK+REST POWER ON

New Devices:1,MacAdd:0xf44efdecd39d,Name:S1 Pro ALL Devices=1 MacAddr=0xf44efdecd39d,Name=S1 Pro

--CMD 2 AT+DISCON | DISCONNECT in case we were connected
OK+DISCON
ALL Devices=0
--CMD 3 AT+DELVMLINK | Delete everything in VMLINK
Delete_Vmlink

Programming Arduino Serial Monitor output | Comments
--CMD 4 AT+REST | RESET so we read and use the new VMLINK table (all empty now)

OK+REST POWER ON

New Devices:1,MacAdd:0xf44efdecd39d,Name:S1 Pro ALL Devices=1 MacAddr=0xf44efdecd39d,Name=S1 Pro

--CMD 5 AT+VMLINK? | Display VMLINK again
OK+VMLINK BT_ADD_NUM=0 BT_NAME_NUM=0 Last_Add=0xf44efdecd39d | all empty
New Devices:1,MacAdd:0xf44efdecd39d,Name:S1 Pro ALL Devices=1 MacAddr=0xf44efdecd39d,Name=S1 Pro New Devices:1,MacAdd:0xf44efdecd39d,Name:S1 Pro CONNECTED ALL Devices=1 MacAddr=0xf44efdecd39d,Name=S1 Pro | NOTE: it says CONNECTED because there is nothing in the VMLINK and it knows how to and did connect to the S1 Pro speaker. It did not connect before because it had VMLINK and it did not match with the speaker.

--- KCX_BT_EMITTER PROGRAMMING STEP COMPLETE ---1 - Scan for Bluetooth receiver devices (such as speaker, headphones, etc.) 2 - Display stored auto-connect Bluetooth receiver devices 3 - Add one auto-connect Bluetooth receiver device to storage 4 - Delete all auto-connect Bluetooth receiver devices from storage ==>

3=ADD | Now we add the S1 Pro MDO to VMLINK

Enter the unique MAC address for the Bluetooth speaker or headphones; it starts with 0x upper or lower case does not matter; maximum of 12 characters after the 0x To abort adding an auto-connect Bluetooth receiver device to storage, just enter an empty line ==>

Your entry "0xf44efdecd39d" was accepted | Get the address from the SCAN

Enter the name you choose for this device; it is OK to place spaces between words maximum of 20 characters total To abort adding an auto-connect Bluetooth receiver device to storage, just enter an empty line ==>

Your entry "S1 Pro MDO" was accepted | Just about any name you want
--CMD 0 AT+ | Now we do a command sequence to add that BT device to VMLINK

OK+

--CMD 1 AT+DISCON
OK+DISCON DISCONNECT

Programming Arduino Serial Monitor output | Comments
--CMD 2 AT+VMLINK? | Display VMLINK
OK+VMLINK BT_ADD_NUM=0 BT_NAME_NUM=0 Last_Add=0xf44efdecd39d | There is nothing in VMLINK before we do our ADD
--CMD 3 AT+ADDLINKADD=0xf44efdecd39d | ADD the MAC Address
OK+ ADDLINKADD VM_MacAdd 1 =0xf44efdecd39d
--CMD 4 AT+ADDLINKNAME=S1 Pro MDO | ADD our name - does not have to match the name the manufacturer gave it

OK+ADDLINKNAME VM_Name 0 =S1 Pro MDO

--CMD 5 AT+REST | We RESET to force it to read and use the modified VMLINK

OK+REST POWER ON

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

--CMD 6 AT+VMLINK? | Make sure we put the right stuff in the VMLINK
OK+VMLINK BT_ADD_NUM=1 BT_NAME_NUM=1 Last_Add=0xf44efdecd39d VM_MacAdd0=0xf44efdecd39d VM_Name0=S1 Pro MDO | OK that is from our ADD
CONNECTED ALL Devices=1 MacAddr=0xf44efdecd39d,Name=S1 Pro | It CONNECTED because (1) it came out of RESET and read VMLINK, (2) it found the device, and (3) it matched the VMLINK address

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

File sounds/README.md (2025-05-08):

# Sounds for the Rubber Band Gun

**Table Of Contents**
* [Top](#sounds-for-the-rubber-band-gun "Top")
* [Sounds from SPACE!!! Colliding Celestial Bodies!](#sounds-from-space-colliding-celestial-bodies "Sounds from SPACE!!! Colliding Celestial Bodies!")
* [Sounds from SPACE!!! Saturn is SO COOL!](#sounds-from-space-saturn-is-so-cool "Sounds from SPACE!!! Saturn is SO COOL!")
* [A few of the Sounds are Recordings of my Family  Members](#a-few-of-the-sounds-are-recordings-of-my-family--members "A few of the Sounds are Recordings of my Family  Members")
* [Text-to-Speech Robotic Sounds](#text\-to\-speech-robotic-sounds "Text-to-Speech Robotic Sounds")
* [Processing Text-to-Speech Robotic Sounds](#processing-text\-to\-speech-robotic-sounds "Processing Text-to-Speech Robotic Sounds")
* [Attributions and Licensing](#attributions-and-licensing "Attributions and Licensing")

## Sounds from SPACE!!! Colliding Celestial Bodies!

Some of my favorite sounds for Rubber Band Gun firing are a sequence similar to the soundified neutron star collisions or black hole collisions.

I particularly like GW170817-template.wav; it has the ramp-up and then the kick at the end, which can be found at https://www.gw-openscience.org/audiogwtc1/. Of course, I would make it just like itself but even more so!!!

Another one I like: Gravitational Waves from a Neutron Star Merger Produced a Signal Detected by LIGO
- https://www.youtube.com/watch?v=CH9JSqUfnSw

Here is a "soundified" rendition of two neutron stars colliding in 2017

- https://qz.com/1103444/ligo-listen-to-a-kilonova-the-sound-of-two-stars-colliding-in-space/

... or maybe from the two black holes colliding in 2015

- https://journals.aps.org/prl/abstract/10.1103/PhysRevLett.116.061102

or a simulation of this. I shamelessly Hollywoodify these sounds!

Thank you LIGO folks for making the fun sounds available to non-researchers!

A very readable one-page comparison of gravity waves to light and sound wave perception is here:
- http://gmunu.mit.edu/sounds/sounds.html

Here are some good articles and overview of LIGO and gravity waves:
- https://www.ligo.org/index.php
- https://www.ligo.org/detections/O1O2catalog.php
- https://www.gw-openscience.org/audiogwtc1/

## Sounds from SPACE!!! Saturn is SO COOL!

Some great science-fictiony sounds came from the Cassini space mission. Here is where you can get audio from the Cassini mission representing radio emissions from Saturn:
- http://www-pw.physics.uiowa.edu/space-audio/cassini/SKR1/
- http://www-pw.physics.uiowa.edu/space-audio/cassini/SKR1/SKR-03-324.wav

This is a phenomenal YouTube showing some of the beautiful images taken from the  Cassini space mission
- "The Final Images Cassini Took" - https://www.youtube.com/watch?v=hxgdjbi2MTU

You can find more about the Cassini mission here
- https://solarsystem.nasa.gov/missions/cassini/overview/

## A few of the Sounds are Recordings of my Family  Members

## Text-to-Speech Robotic Sounds

The Rubber Band Gun speaks to you when you want to configure the sounds or LED patterns. 
I used the "original" eSpeak text-to-speech program version 1.48.04. This produces sounds with a robotic flavor, which I wanted.

The original eSpeak text to speech code and compiled versions can be found at http://espeak.sourceforge.net/
- Kudos to (email) jonsd at users dot sourceforge dot net for creating eSpeak

Note that eSpeak project is inactive since disappearance of Jonathan Duddington.

Active development and support now happens in eSpeak NG project https://github.com/espeak-ng/espeak-ng, maintained by Reece H. Dunn.
- Kudos to Reece H. Dunn for continuing the good work

A web implementation of eSpeak can be found as below; it is great fun, and just one of many text-to-text and text-to-speech engines on the site. https://lingojam.com/RobotVoiceGenerator

## Processing Text-to-Speech Robotic Sounds

I used my program RobotSounds.py to read StateTable_minimal.xlsx (which contains the text to generate) and make a Linux "bash" script that makes the sounds.
- The bash script generates all the individual *.wav sound files and also a combined totString.wav.
- - totString.wav separates the sounds by having "Ah. Ah. Ah." between each one so I could find the boundaries.
- - You can do the Audacity processing either one at a time or using the totString.wav file, but you need to have individual numbered files when done.
- - See https://github.com/Mark-MDO47/AudioPlayer-YX5200 for more information about the file numbering scheme
- - The bash file invokes the "original" eSpeak program version 1.48.04.
- I think the bash file could easily be converted to a Windows *.bat file. That is left as an exercise for the reader.

After creating the text-to-speech audio file(s), this is how I processed them to make them even more robotic:
- import file in Audacity, set to mono if not already set (File->Import->Audio)
- duplicate the track (select track, then Edit->Duplicate)
- reverse one of the tracks (select track, then Effect->Reverse)
- select reversed track and change pitch (Effect->ChangePitch, choose -2 semitones)
- for both tracks one at a time, echo effect (Effect->Echo, choose DelayTime about 0.01 sec and DecayFactor about 0.5)
- select reversed track and reverse it back to normal order (select track, then Effect->Reverse)
- select both tracks (ctrl-A) then render (Tracks->Mix->MixAndRender)
- export as 22050Hz mono, "WAV (microsoft) signed 16-bit PCM" (File->Export->ExportAsWav or for more options File->Export->ExportAudio)

Audacity can be found at https://www.audacityteam.org/

Once you have the individual numbered *.wav files collected (both text to speech and all the others), they need to be stored on an SD card very precisely. For details, see the description of copyem.py in https://github.com/Mark-MDO47/AudioPlayer-YX5200

## Attributions and Licensing

Here are the Creative Commons licenses in the non-speech sound files I used:

| Tag | Name | URL |
| --- | --- | --- |
| zero/1.0/	| Creative Commons 0 License | https://creativecommons.org/publicdomain/zero/1.0/ |
| by/3.0/	| Creative Commons Attribution License | https://creativecommons.org/licenses/by/3.0/ |
| by-nc/3.0/ | Creative Commons Attribution Noncommercial License | https://creativecommons.org/licenses/by-nc/3.0/ |

Here are the sound files I used, modified, and combined for the prototype sounds:

| Tag | File Name | URL | Who |
| --- | --- | --- | --- |
| N/A | GW170817-template.wav | https://www.gw-openscience.org/audiogwtc1/ | LIGO detectors |
| N/A |	SKR-03-324.wav |	http://www-pw.physics.uiowa.edu/space-audio/cassini/SKR1/ |	NASA Cassini mission Radio and Plasma Wave Science |
| zero/1.0/ | 407052__sojan__power-charge.flac | https://freesound.org/s/193610/ | crashoverride61088 |
| zero/1.0/ |	397254__screamstudio__loading.wav |	https://freesound.org/s/397254/ | ScreamStudio |
| zero/1.0/	| 145209__lensflare8642__shotgun-sounds.mp3	| https://freesound.org/s/145209/ | lensflare8642 |
| by/3.0/ | 216096__richerlandtv__u-f-o.mp3 | https://freesound.org/s/216096/ | RICHERlandTV |
| by/3.0/ | 88635__uair01__bicycle-picture-in-spectrum.wav | https://freesound.org/s/88635/ | uair01 |
| by/3.0/ | 7967__cfork__boing-raw.aiff | https://freesound.org/s/7967/ | cfork |
| by/3.0/	| 383205__spiceprogram__loading-sound.wav	| https://freesound.org/s/383205/ | SpiceProgram  |
| by-nc/3.0/ | 179281__timbre__boingy-sweep.flac | https://freesound.org/s/179281/ | Timbre |
| zero/1.0/ | 380886__morganpurkis__doom-shotgun-2017.wav | https://freesound.org/s/380886/ | morganpurkis |
| zero/1.0/ | 500418__dj-somar__intro-reverso-craver-microbrute.wav | https://freesound.org/s/500418/ | DJ_SoMaR |
| by/3.0/ | 272068__ichbinjager__shotgun-action.wav | https://freesound.org/s/272068/ | IchBinJager |
| by/3.0/ | 431117__inspectorj__door-front-opening-a.wav | https://freesound.org/s/431117/ | inspectorj |
| zero/1.0/ | 404068__swordofkings128__backyard-gate-open.wav | https://freesound.org/s/404068/ | swordofkings128 |
| by/3.0/ | 96964__gabisaraceni__porta-abrindo-5.wav | https://freesound.org/s/96964/ | gabisaraceni |
| by/3.0/ | 275537__wjoojoo__contact-mic-on-satellite-dish04.wav | https://freesound.org/s/275537/ | wjoojoo |
| zero/1.0/ | 352852__josepharaoh99__game-style-laser-beam.wav | https://freesound.org/s/352852/ | josepharaoh99 |
| by/3.0/ | 417363__xcreenplay__boing-massive-kick.wav | https://freesound.org/s/417363/ | xcreenplay |
| by/3.0/ | 221875__hero-of-the-winds__spring-boing.wav | https://freesound.org/s/221875/ | hero-of-the-winds |
| by/3.0/ | 240297__jalastram__abstract-guitar-sfx-003.wav | https://freesound.org/s/240297/ | jalastram |
| zero/1.0/ | 383760__deleted-user-7146007__laboratory-mad-scientist-science-fiction-sci-fi.wav | https://freesound.org/s/383760/ | deleted-user-7146007 |
| by/3.0/ | 417131__cuddlenucks__science-fiction-noise-3.wav | https://freesound.org/s/417131/ | cuddlenucks |
| zero/1.0/ | 170136__lazr2012__machinery-bo.flac | https://freesound.org/s/170136/ | lazr2012 |
| by/3.0/ | 169292__lazr2012__haywirefusionator.ogg | https://freesound.org/s/169292/ | lazr2012 |
| by-nc/3.0/ | 165483__timbre__glitch-voice-ep-mp3.mp3 | https://freesound.org/s/165483/ | timbre |
| zero/1.0/ | 162814__timgormly__spaceship-4.aiff | https://freesound.org/s/162814/ | timgormly |
| by-nc/3.0/ | 91296__timbre__bwaang-2-reverb.mp3 | https://freesound.org/s/91296/ | timbre |
| zero/1.0/ |	388276__csnmedia__la-cucaracha-car-horn.wav |	https://freesound.org/s/388276/ |	csnmedia |
| zero/1.0/ |	118807__lmbubec__17-1985-ford-mustang-horn.wav |	https://freesound.org/s/118807/ |	lmbubec |

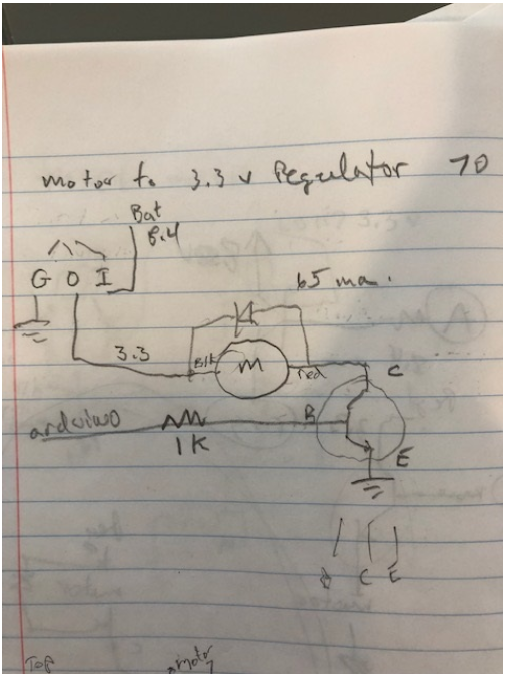
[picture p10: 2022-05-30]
3D_model/schematic_sidewinder.png

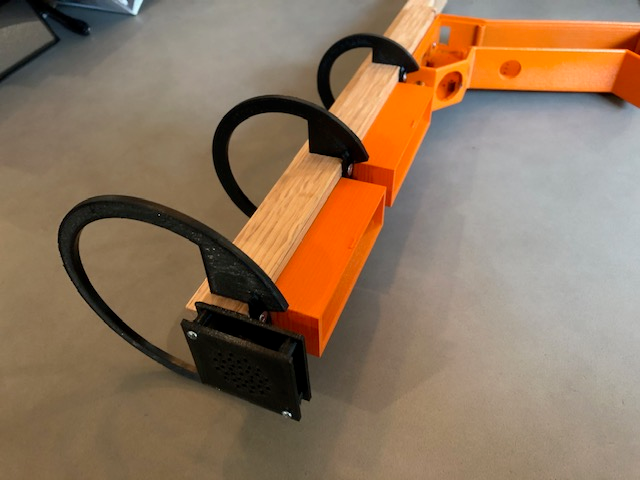
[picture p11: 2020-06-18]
3D_model/IMG_2208_orange.png

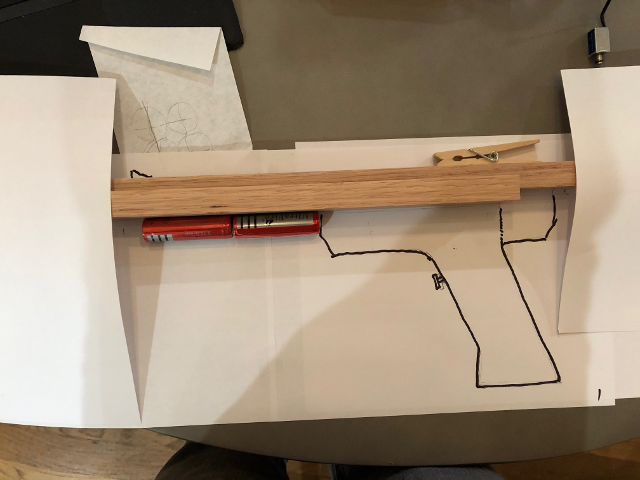
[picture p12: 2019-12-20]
3D_model/mockup.png

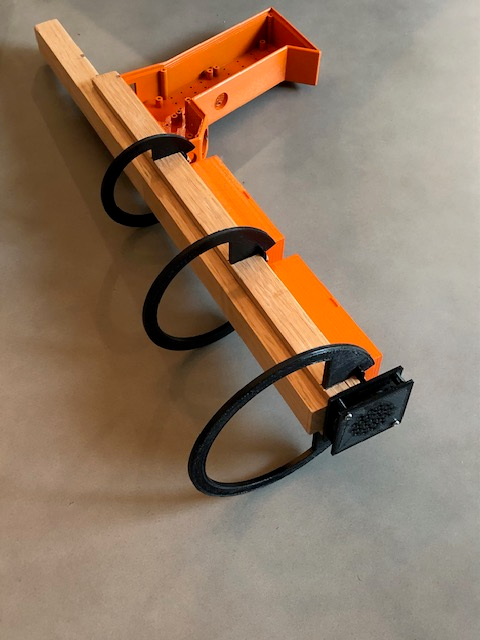
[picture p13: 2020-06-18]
3D_model/IMG_2209_orange.png

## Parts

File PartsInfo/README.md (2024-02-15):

# Parts Info

**Table Of Contents**
* [Top](#parts-info "Top")
* [Arduino Nano and ATMEGA 328P](#arduino-nano-and-atmega-328p "Arduino Nano and ATMEGA 328P")
* [Sound Module](#sound-module "Sound Module")
* [Bluetooth Module](#bluetooth-module "Bluetooth Module")
* [WS2812 LED and serial communications](#ws2812-led-and-serial-communications "WS2812 LED and serial communications")

## Arduino Nano and ATMEGA 328P
Lots of info on the Arduino Nano is found here (diagrams, not schematics)
* https://www.circuitstoday.com/arduino-nano-tutorial-pinout-schematics

The ATMEGA 328P chip used in the Arduino Nano is described here
* http://ww1.microchip.com/downloads/en/DeviceDoc/ATmega48A-PA-88A-PA-168A-PA-328-P-DS-DS40002061A.pdf

Mapping the ports to the internal registers is described here
* https://www.arduino.cc/en/Reference/PortManipulation

## Sound Module
The YX5200 uses FAT32-formatted TF or microSD card up to 32 GByte. It can play multiple sound file formats including *.wav and *.mp3

Information on the YX5200 sound module and my experience with it can be found in either of these places
* https://github.com/Mark-MDO47/RubberBandGun/blob/master/PartsInfo/YX5200.md
* https://github.com/Mark-MDO47/AudioPlayer-YX5200

Best datasheet I could find on the YX5200 chip is found here
* https://github.com/PowerBroker2/DFPlayerMini_Fast/blob/master/extras/FN-M16P%2BEmbedded%2BMP3%2BAudio%2BModule%2BDatasheet.pdf

These look like a helpful sites for the YX5200:
* https://wiki.dfrobot.com/DFPlayer_Mini_SKU_DFR0299
* https://github.com/DFRobot/DFRobotDFPlayerMini

This one is a re-write of the DFRobot library; also includes an English language spec sheet in the "extras" directory.
* https://https://github.com/PowerBroker2/DFPlayerMini_Fast

## Bluetooth Module
Get tips and some code for programming the KCX_BT_EMITTER Bluetooth Audio Transmitter module
* https://github.com/Mark-MDO47/BluetoothAudioTransmitter_KCX_BT_EMITTER

Information on the Bluetooth audio transmitter module is found here (along with ordering info)
* https://www.aliexpress.com/item/33058710334.html

Best information on the Bluetooth module I could find is here; need to translate from Chinese (see next link)
* https://item.taobao.com/item.htm?spm=a21wu.12321156-tw.0.0.7e76d1c7xEOcFZ&id=570274835710

Some more usage info on the Bluetooth module, especially English information on controlling with serial AT commands
* https://www.electro-tech-online.com/threads/kcx_bt_emitter-low-cost-bluetooth-bt-audio-module.158156/

## WS2812 LED and serial communications
FastLED is the library I use for controlling these color addressable LEDs
* https://www.arduino.cc/reference/en/libraries/fastled/
* https://github.com/FastLED/FastLED

If you are new to FastLED, look at this famous demo code to see how easy it can be
* https://github.com/FastLED/FastLED/blob/master/examples/DemoReel100/DemoReel100.ino

Information on the WS2812B is found here
* https://cdn-shop.adafruit.com/datasheets/WS2812B.pdf

The dimensions of the particular ring we used is found here
* https://github.com/Mark-MDO47/RubberBandGun/blob/master/PartsInfo/LED_Dimensions.png

A top-level description of the WS2812B serial protocol (per spec) is found here
* https://www.arrow.com/en/research-and-events/articles/protocol-for-the-ws2812b-programmable-led

Information on doing quick WS2812B I/O is found here (I didn't wind up using it but it was fascinating)
* https://wp.josh.com/2014/05/13/ws2812-neopixels-are-not-so-finicky-once-you-get-to-know-them/
* https://github.com/bigjosh/SimpleNeoPixelDemo

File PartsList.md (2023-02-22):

# Parts List

| Num | CostEach | CostTotal | Description | Source |
| --- | --- | --- | --- | --- |
| 1 | $0.00 | $0.00 | clothespin in homage to rubber band guns everywhere | N/A |
| 1 | $0.80 | $0.80 | power switch, equivalent of: | https://www.futureelectronics.com/p/electromechanical--switches--rocker/rr511d1121-e-switch-1057563 |
| 1 | $0.70 | $0.70 | trigger button, equivalent of: | https://smile.amazon.com/Pieces-Waterproof-Momentary-Button-Switch/dp/B07PG8YYWK |
| 2 | $23.99 | $47.98 | sets of 5050 WS2812B LED rings, one facing forward and one facing back: | https://smile.amazon.com/gp/product/B07437X7SL |
| 1 | $2.00 | $2.00 | V3.0 ATmega328P 5V 16M CH340 Compatible to Arduino Nano V3 with 32Kbyte Flash (program storage), 2Kbyte SRAM, 1Kbyte EEPROM: source: my spare parts bin, so some very old ones... but available many places including: | https://www.aliexpress.com/item/32242048437.html |
| 1 | $0.40 | $0.40 | SN74HCT125N quadruple bus buffer so one clone Arduino Nano can drive both sets of WS2812B rings: | https://www.digikey.com/product-detail/en/texas-instruments/SN74HCT125N/296-8386-5-ND/376860 |
| 1 | $4.40 | $4.40 | UBEC 3Amp: | https://smile.amazon.com/2-Pieces-Hobbywing-Switch-mode-UBEC-Helicopter-Quadcopter/dp/B01GHMW0C0 |
| 2 | $4.50 | $8.99 | Button top 18650 Rechargeable Batteries: | https://smile.amazon.com/dp/B08LKP5LPD |
| 1 | $2.60 | $2.60 | YX5200 sound player: | https://smile.amazon.com/Anmbest-YX5200-DFPlayer-Supporting-Arduino/dp/B07JGWMPTF/ |
| 1 | $2.49 | $2.49 | small speaker: | https://smile.amazon.com/Uxcell-a15080600ux0275-Internal-Magnet-Speaker/dp/B0177ABRQ6/ |
| 1 | $3.80 | $3.80 | 16Gbyte SD card for YX5200: | https://smile.amazon.com/Patriot-16GB-Micro-SDHC-PSF16GMCSDHC5PK/dp/B013P27MDW |
| 1 | $3.55 | $3.55 | KCX_BT_EMITTER BlueTooth audio transmitter: | https://www.aliexpress.com/item/33058710334.html |
| 1 | $35.99 | $35.99 | ZoeeTree S1Pro Bluetooth Speaker 20W , IPX7 Waterproof, for the RBG: | https://smile.amazon.com/gp/product/B088H56DNY/ (link expired) |
| 1 | $0.95 | $0.95 | Mini On/Off Push-Button Switch: | https://www.adafruit.com/product/3870 |
| 3 | $0.08 | $0.24 | colored push-buttons for configuration of effects: | https://www.amazon.com/gp/product/B07C7211PJ/ref=ppx_yo_dt_b_asin_image_o08_s00 |
| 1 | $0.69 | $0.69 | 4610X-AP1-103LFCT-ND RES ARRAY 9 RES 10K OHM 10SIP - for pull-up resistors: | https://www.digikey.com/en/products/detail/bourns-inc/4610X-AP1-103LF/3741070 |
| 2 | $0.10 | $0.20 | 220 Ohm resistor, 1/4 watt (optional): | https://www.digikey.com/en/products/detail/stackpole-electronics-inc/CF14JT220R/1741346 |
| 1 | $0.84 | $0.84 | 1K Ohm resistor, 1/4 watt (absolutely needed): | https://www.digikey.com/en/products/detail/ohmite/OD102JE/823687 |
| 1 | $0.71 | $0.71 | USB 2.0 Breakout Board type A Female | https://www.amazon.com/Breakout-MELIFE-Adapter-2-54mm-Pinboard/dp/B07W7XMV3W |
| 1 | $0.71 | $0.71 | USB 2.0 Breakout Board type A Male | https://www.amazon.com/MELIFE-Converter-2-54mm-Adapter-Breadboard/dp/B07W6T9KPJ |
| --- | --- | --- | --- | --- |
| 0 | $0.00 | $0.00 | driver circuit for selenoid: | https://cdn-shop.adafruit.com/product-files/412/solenoid_driver.pdf |
| 1 | $14.29 | $14.29 | small solenoid for rubber-band release coordinated with sound/light effects: | https://www.amazon.com/gp/product/B07TKTG3BH/ref=ox_sc_act_title_1?smid=A1THAZDOWP300U&psc=1 |
| 1 | $0.83 | $0.83 | TIP120 Power Darlington Transistor: | https://www.adafruit.com/product/976 |
| 1 | $0.10 | $0.10 | 1N4004 diode 1A 400V: | https://www.digikey.com/en/products/detail/nte-electronics-inc/1N4004/11645015 |
| 1 | $0.10 | $0.10 | 2.2K Ohm resistor, 1/4 watt: | https://www.digikey.com/en/products/detail/stackpole-electronics-inc/RNMF14FTC2K20/2617325 |
| --- | --- | --- | --- | --- |
| 0 | $0.00 | $0.00 | driver circuit for motor (SIDEWINDER): |  |
| 1 | $9.86 | $9.86 | Mini Motor Low-speed Gearbox (4-speed) by Tamiya 70189**860.  assembled with 661.2:1 gear ratio | https://www.robotshop.com/en/tamiya-4-speed-mini-gearbox-motor.html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 |
| 1 | $1.25 | $1.25 | 3.3V 800mA Linear Voltage Regulator - LD1117-3.3 TO-220. | https://www.adafruit.com/product/2165 |
| 1 | $0.15 | $0.15 | Diode, 1N4001 | https://www.adafruit.com/product/755 |
| 1 | $0.84 | $0.84 | 1K ohm 1/4 watt resistor | https://www.digikey.com/en/products/detail/ohmite/OD102JE/823687 |

Total cost (without wood or 3D printer parts or wire)
* $133.37 - SOLENOID (SINGLETON)  version
* $130.14 - MOTOR (SIDEWINDER) version
- but about $36 of that cost is the bluetooth speaker which you may have or not need

The barrel of the Rubber Band Gun is made from wood, with a sliding barrel attachment to assist in stringing the rubber band through the LED rings. The rest including the handgrip is 3-D printed. The clear cover for the handgrip is laser-cut acrylic; there is another acrylic board inside.

# Audio Player Part
The YX5200 uses FAT32-formatted TF or microSD card up to 32 GByte

These look like some helpful sites for the YX5200:
* https://wiki.dfrobot.com/DFPlayer_Mini_SKU_DFR0299
* https://github.com/DFRobot/DFRobotDFPlayerMini

This one is a re-write of the DFRobot library; also includes an English language spec sheet in the "extras" directory.
* https://github.com/PowerBroker2/DFPlayerMini_Fast

For a description of my experiences with using this module (I had some challenges), see the Readme.md in https://github.com/Mark-MDO47/RubberBandGun/tree/master/RBG_arduino.

# Bluetooth Transmitter Part
The KCX_BT_EMITTER Bluetooth Audio Transmitter Module receives line-level (not speaker-level) stereo audio in and transmits to a Bluetooth receiver (speaker, headphones, etc.). Be sure to connect the analog ground and do not connect analog ground to digital ground. Also due to latency in packetizing/depacketizing the Bluetooth audio, it is best to turn off the built-in speaker on the RBG if using the Bluetooth audio.

The Bluetooth Module uses an "AT" command set to program it to connect to your speaker and not others. Included in this repository is an Arduino sketch for a 2nd Arduino that is used to program the KCX_BT_EMITTER in-place. The following document describes using this capability:
* https://github.com/Mark-MDO47/RubberBandGun/blob/master/ProgrammingArduino_SerialMonitor_SampleOutput.pdf

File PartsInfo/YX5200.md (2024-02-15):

# YX5200 Audio Module

**Table Of Contents**
* [Top](#yx5200-audio-module "Top")
* [Resources](#resources "Resources")
* [My Experiences](#my-experiences "My Experiences")
* [WAV_hdr_YX5200.py](#wav_hdr_yx5200py "WAV_hdr_YX5200.py")
* [copyem.py](#copyempy "copyem.py")
* [Extras:](#extras "Extras:")

## Resources
Files to help with using YX5200 can be found here:

https://wiki.dfrobot.com/DFPlayer_Mini_SKU_DFR0299

https://github.com/DFRobot/DFRobotDFPlayerMini

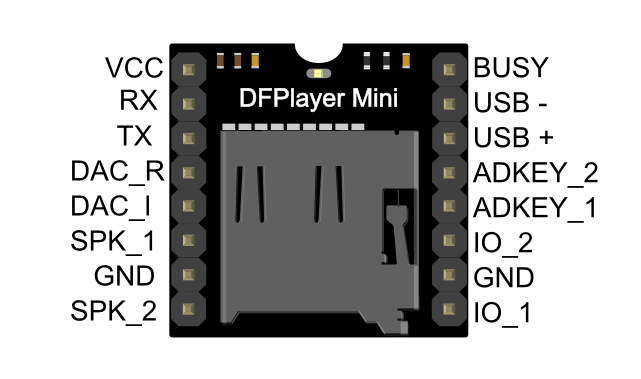
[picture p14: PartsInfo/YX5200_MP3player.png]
Top view pin arrangement on YX5200 module

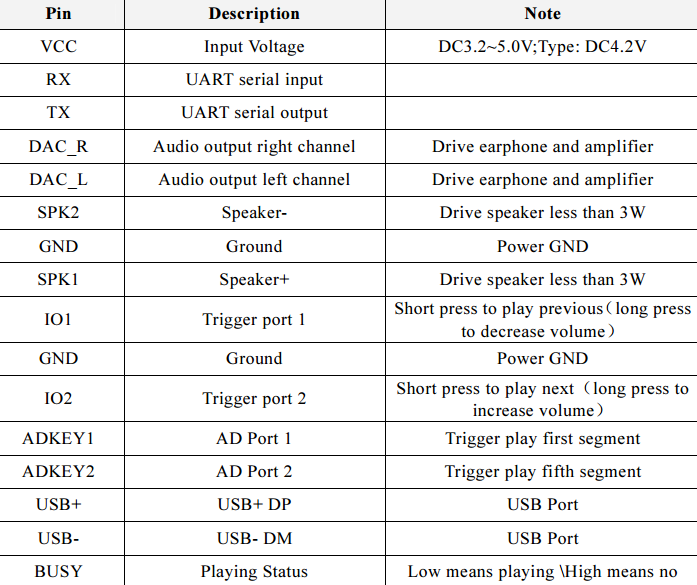
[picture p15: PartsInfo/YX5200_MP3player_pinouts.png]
Description of pins on YX5200 module


## My Experiences

Here is a description of my experiences using the YX5200 module (I had some challenges)

You definitely want to use the 1K resistor on the TX line or you can distinctly hear clicks during serial communication.

My experience (these comments apply to the modules I used)
- with a chip labelled MH-ETLIVE MH2024K-24SS) on ORANGE SIDEWINDER RBG:
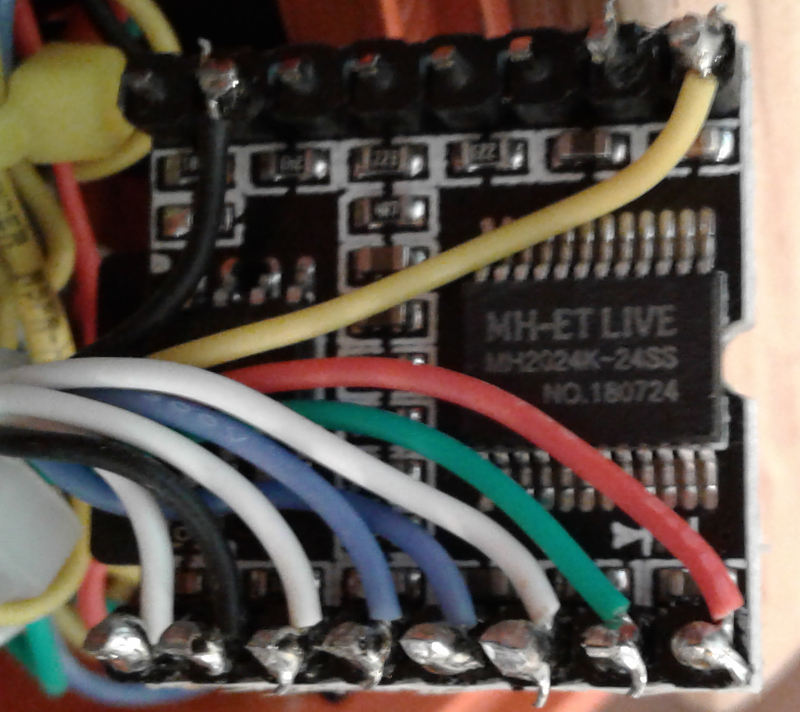
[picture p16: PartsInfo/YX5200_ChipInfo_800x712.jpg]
YX5200 Chip MH-ETLIVE MH2024K-24SS used in ORANGE SIDEWINDER RBG

- with a chip labelled JC AA20HFJ616-94 on SILVER SOLENOID SINGLETON RBG (note: lump on green wire is 1K Ohm resistor):
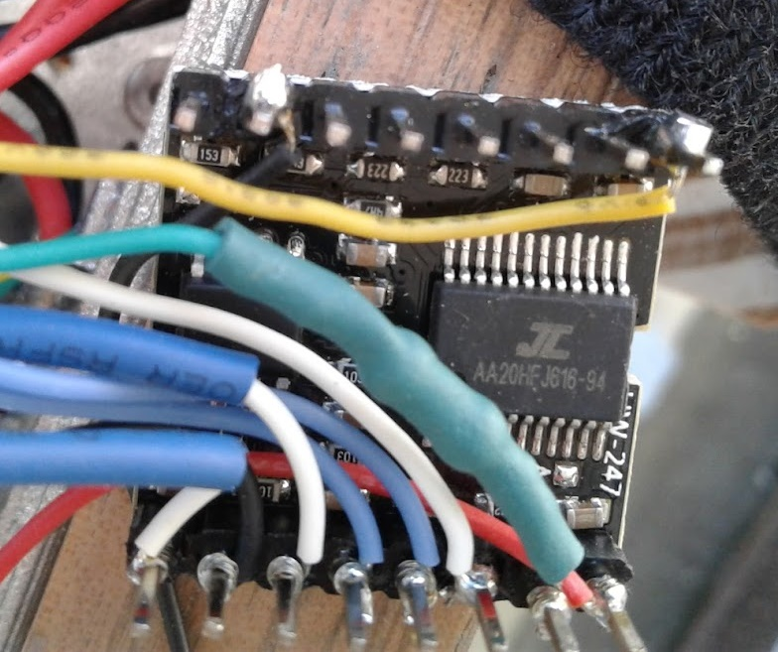
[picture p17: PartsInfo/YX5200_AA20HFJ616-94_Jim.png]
YX5200 Chip JC AA20HFJ616-94 used in SILVER SOLENOID SINGLETON RBG

- Using .playMp3Folder() worked on the first few calls but I had trouble making it work when interrupting a playing sound. I tried a bunch of things (but not every combination) and finally gave it up and now use the most basic of functions .play().
  - Also *.wav files start faster after a command to play. Apparently there is some overhead to start an *.mp3 file. It was a small delay but noticeable in the RBG project.
  - Because the .play() function requires specific filenames and orders of file copies, I wrote copyem.py to help me get the files into the SD card in the correct order.
- While doing the above experiments I had the impression that turning ACK on (default at this time) made it more likely to have the trouble above. I turned ACK off in the .begin(mySoftwareSerial, false, true) call.
- Sometimes there was a delay in the BUSY pin registering after starting a sound. So far all the delays I have documented were <= 40 milliseconds. Since my code wants to do things (LED-related) faster than that, I put in code to force a fake BUSY for the first 250 milliseconds after starting a sound. Probably overkill.
- Some of my readings indicate that there are knock-off clones of the YX5200 module that may not implement all the functions properly. My guess would be that they have an out-of-date set of firmware. At least some of these clones used a red LED to indicate sound playing instead of the blue LED used on the genuine YX5200. My modules did have a blue LED, but this is not necessarily a guarantee that they were genuine, so it is possible the problems I had were due to using a knock-off clone.
- Both grounds on the YX5200 are marked as digital ground, but I found that if I connected them together the line output had a buzz (didn't hear it on speaker output). I got better results when I pretended that the GND between SPK1 and SPK2 was an analog ground. Seems to be mostly for "Line outputs"; the speaker output is mono sound.
- YX5200s work with integer 16 bit PCM at frequencies 22.050 KHz, 44.100 KHz, and 48.000 KHz
- YX5200 DOES NOT WORK with 96.000 KHz, will just skip the file

There have been a lot of reactions to clone modules and difficulties with serial communication and audio noise. Here is an excellent resource on this subject

https://www.thebackshed.com/forum/ViewTopic.php?TID=11977&P=1

## WAV_hdr_YX5200.py
This routine allows checking of *.wav files to see if they are the correct format for using with the YX5200.
- https://github.com/Mark-MDO47/RubberBandGun/blob/master/WAV_hdr_YX5200/WAV_hdr_YX5200.py

Below is the help text from WAV_hdr_YX5200.py.<br>
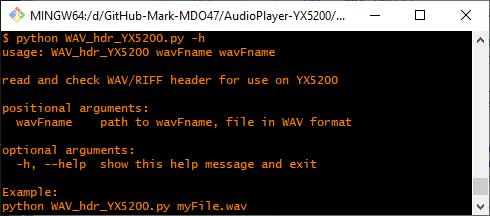
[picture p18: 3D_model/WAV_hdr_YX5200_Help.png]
Help text for WAV_hdr_YX5200.py


Below is an example use of WAV_hdr_YX5200.py.<br>
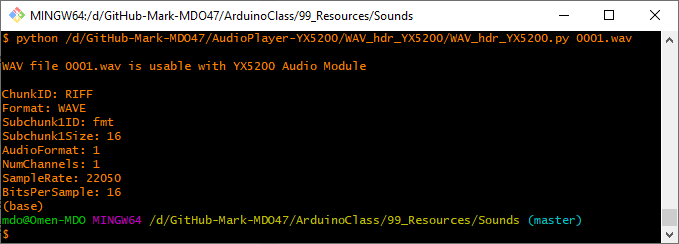
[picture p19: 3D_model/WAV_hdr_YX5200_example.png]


## copyem.py

This is a routine that makes it much easier to create SD cards that work with the .play() routine. Below is the help text from copyem.py.

Note: I run this routine in GIT bash on Windows 10, so I use the H: (or other letter) to access the drive but use the / separator for directories.

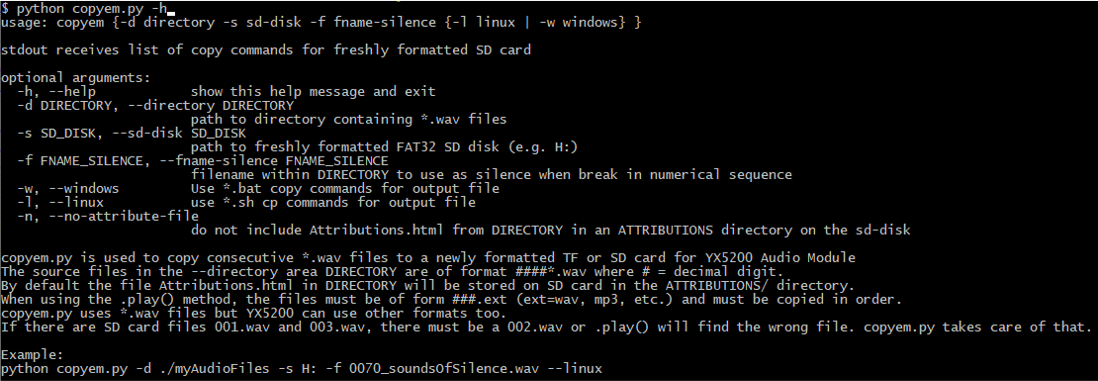
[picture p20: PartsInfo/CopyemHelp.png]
Help text for copyem.py


It is OK to copy to the SD card using names like 001_this_is_a_test.wav, but if the names get longer than 8.3 then the directory gets more complicated and it might affect the speed of starting a sound eventually, so I just copied the number such as 001.wav.

So the sequence is:
- Put your ####*.wav files in a directory. For this example I will use the directory ./myAudioFiles
- - NOTE: I use # to indicate a decimal digit from 0 through 9
- Also make a ####*.wav file that is just a second or two of silence and place that in ./myAudioFiles
- Optionally make a Attributions.html file for attributions and place that in ./myAudioFiles
- Connect an SD-card that is 32 gigabytes or less and FAT-32 format the SD-card. In this example it will be on H:
- - NOTE: it MUST be freshly FAT-32 formatted; do not try to re-use SD card without formatting. There are many ways to do this; I use https://www.sdcard.org/downloads/formatter/

At this point, ./myAudioFiles has the following (short list of *.wav to make it readable)
- 0001_first.wav
- 0003_third.wav
- 0005_silence.wav
- Attributions.html

Run the program as follows
- python copyem.py -d ./myAudioFiles -s H: -f 0005_silence.wav > mycopy.sh

It will output the following (note: a blank line before attribution is omitted here)
- cp ./myAudioFiles/0001_first.wav H:/001.wav
- cp ./myAudioFiles/0005_silence.wav H:/002.wav
- cp ./myAudioFiles/0003_third.wav H:/003.wav
- cp ./myAudioFiles/0005_silence.wav H:/004.wav
- cp ./myAudioFiles/0005_silence.wav H:/005.wav
- mkdir H:/ATTRIBUTIONS
- cp  ./myAudioFiles/Attributions.html H:/ATTRIBUTIONS

Alternatively, "python copyem.py -d ./myAudioFiles -s H: -f 0005_silence.wav --windows > mycopy.bat" will output the following
- copy .\myAudioFiles\0001_first.wav H:\001.wav
- copy .\myAudioFiles\0005_silence.wav H:\002.wav
- copy .\myAudioFiles\0003_third.wav H:\003.wav
- copy .\myAudioFiles\0005_silence.wav H:\004.wav
- copy .\myAudioFiles\0005_silence.wav H:\005.wav
- mkdir H:\ATTRIBUTIONS
- copy  .\myAudioFiles\Attributions.html H:\ATTRIBUTIONS

Then either source mycopy.sh or run mycopy.bat, eject the SD card, and insert it into the YX5200.

## Extras:
Check out https://https://github.com/PowerBroker2/DFPlayerMini_Fast for a re-write (much simplified) of the DFRobot routines. I continued using the DFRobot routines for this project since by the time I found the other I had a lot of experience with the DFRobot routines.

That area also includes the PDF file I copied into my https://github.com/Mark-MDO47/RubberBandGun/tree/master/RBG_arduino/YX5200_info directory; that is the best information on the chip that forms the basis of the YX5200 module that I have seen.

This README describes using the YX5200 on the Rubber Band Gun. My repository on the YX5200 itself is more tuned to general usage of YX5200
* https://github.com/Mark-MDO47/AudioPlayer-YX5200

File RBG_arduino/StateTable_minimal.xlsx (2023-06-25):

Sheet: Sounds
usage | num | File Name | Description | all usage | License | Who | URL | Mnemonic | calc1 | calc2 | #define
windup | 1 | 383205__spiceprogram__loading-sound.wav | very good windup sound with kaching at end | windup | by/3.0/ | SpiceProgram | https://freesound.org/s/383205/
windup | 2 | 397254__screamstudio__loading.wav | very cute - roboty - has long steady tail that could also be used | windup | zero/1.0/ | screamstudio | https://freesound.org/s/397254/
windup | 3 | 88635__uair01__bicycle-picture-in-spectrum.wav | split for windup, waiting | windup waiting | by/3.0/ | uair01 | https://freesound.org/s/88635/
windup | 4 | 407052__sojan__power-charge.flac | straight crescendo - jet + machine | windup | zero/1.0/ | sojan | https://freesound.org/s/193610/
windup | 5 | 0005__mdo47__Gravitational-Waves-from-a-Neutron-Star-Merger-Produced-a-Signal-Detected-by-LIGO_mdo47.wav | mdo47 combination windup; max license is by/3.0/ | windup | by/3.0/ | mdo47 | local
windup | 6 | 275537__wjoojoo__contact-mic-on-satellite-dish04.wav | percussiony - like train at start, end might make shooting sound | shoot | by/3.0/ | wjoojoo | https://freesound.org/s/275537/
windup | 7 | 388276__csnmedia__la-cucaracha-car-horn.wav | La Cucaracha car horn | windup, open, lock/load | zero/1.0/ | csnmedia | https://freesound.org/s/388276/
shoot | 11 | 352852__josepharaoh99__game-style-laser-beam.wav | good shooting laser sound | shoot | zero/1.0/ | josepharaoh99 | https://freesound.org/s/352852/
shoot | 12 | 7967__cfork__boing-raw.aiff | boing shooting sound | shoot | by/3.0/ | cfork | https://freesound.org/s/7967/
shoot | 13 | 275537__wjoojoo__contact-mic-on-satellite-dish04.wav | percussiony - like train at start, end might make shooting sound | shoot | by/3.0/ | wjoojoo | https://freesound.org/s/275537/
shoot | 14 | 417363__xcreenplay__boing-massive-kick.wav | science fictiony multiple shots - maybe use a fraction of it for shooting | shoot | by/3.0/ | xcreenplay | https://freesound.org/s/417363/
shoot | 15 | 91296__timbre__bwaang-2-reverb.mp3 | some nice BWAAA sounds | shoot | by-nc/3.0/ | timbre | https://freesound.org/s/91296/
shoot | 16 | 145209__lensflare8642__shotgun-sounds.mp3 | several shotgun lock/load plus some fire sounds; last fire is good (breaking glass) | lock/load open shoot | zero/1.0/ | lensflare8642 | https://freesound.org/s/145209/
shoot | 17 | 0017__mdo47__lPewPewPew.wav | mdo47 "L" recording of "Pew-pew... pew-pew... pew!" | shoot | by/3.0/ | mdo47 | local
shoot | 18 | 0018__mdo47__mPewPewPew.wav | mdo47 "M" recording of "Pew pew pew... pew-pew-pew-pew pew!" | shoot | by/3.0/ | mdo47 | local
shoot | 19 | 0019__mdo47__iPewPewPew.wav | mdo47 "I" recording of "Pew... pew-pew!" | shoot | by/3.0/ | mdo47 | local
open | 21 | 431117__inspectorj__door-front-opening-a.wav | maybe the best "open" sound | lock/load open | by/3.0/ | inspectorj | https://freesound.org/s/431117/
open | 22 | 404068__swordofkings128__backyard-gate-open.wav | really good lock/load or open | lock/load open | zero/1.0/ | swordofkings128 | https://freesound.org/s/404068/
open | 23 | 272068__ichbinjager__shotgun-action.wav | good loud lock/load | lock/load open | by/3.0/ | IchBinJager | https://freesound.org/s/272068/
open | 24 | 96964__gabisaraceni__porta-abrindo-5.wav | good opening; includes squeaky hinge at end | lock/load open | by/3.0/ | gabisaraceni | https://freesound.org/s/96964/
open | 25 | 145209__lensflare8642__shotgun-sounds.mp3 | several shotgun lock/load plus some fire sounds; last fire is good | lock/load open shoot | zero/1.0/ | lensflare8642 | https://freesound.org/s/145209/
open | 26 | 380886__morganpurkis__doom-shotgun-2017.wav | 2nd part has lock/load | lock/load open | zero/1.0/ | morganpurkis | https://freesound.org/s/380886/
open | 27 | 388276__csnmedia__la-cucaracha-car-horn.wav | La Cucaracha car horn | windup, open, lock/load | zero/1.0/ | csnmedia | https://freesound.org/s/388276/
lock/load | 31 | 431117__inspectorj__door-front-opening-a.wav | maybe the best "open" sound | lock/load open | by/3.0/ | inspectorj | https://freesound.org/s/431117/
lock/load | 32 | 404068__swordofkings128__backyard-gate-open.wav | really good lock/load or open | lock/load open | zero/1.0/ | swordofkings128 | https://freesound.org/s/404068/
lock/load | 33 | 272068__ichbinjager__shotgun-action.wav | good loud lock/load | lock/load open | by/3.0/ | IchBinJager | https://freesound.org/s/272068/
lock/load | 34 | 96964__gabisaraceni__porta-abrindo-5.wav | good opening; includes squeaky hinge at end | lock/load open | by/3.0/ | gabisaraceni | https://freesound.org/s/96964/
lock/load | 35 | 145209__lensflare8642__shotgun-sounds.mp3 | several shotgun lock/load plus some fire sounds; last fire is good | lock/load open shoot | zero/1.0/ | lensflare8642 | https://freesound.org/s/145209/
lock/load | 36 | 380886__morganpurkis__doom-shotgun-2017.wav | 2nd part has lock/load | lock/load open | zero/1.0/ | morganpurkis | https://freesound.org/s/380886/
lock/load | 37 | 388276__csnmedia__la-cucaracha-car-horn.wav | La Cucaracha car horn | windup, open, lock/load | zero/1.0/ | csnmedia | https://freesound.org/s/388276/
PowerOn | 41 | 0041__mdo47__lFOOF_Darling.wav | mdo47 recording of "This is the awesome FOOF Rubber Band Gun, darling." | PowerOn | by/3.0/ | mdo47 | local | mEFCT_PWRON_LFOOF | 17 | #define mEFCT_PWRON_LFOOF 41 // This is the awesome FOOF Rubber Band Gun, darling.
PowerOn | 42 | 0042__mdo47__mFOOF.wav | mdo47 recording of "This is the awesome FOOF Rubber Band Gun." | PowerOn | by/3.0/ | mdo47 | local | mEFCT_PWRON_MFOOF | 17 | #define mEFCT_PWRON_MFOOF 42 // This is the awesome FOOF Rubber Band Gun.
PowerOn | 43 | 0043__mdo47__cFOOF_Achtung.wav | mdo47 recording of "Achtung! This is the awesome FOOF Rubber Band Gun." | PowerOn | by/3.0/ | mdo47 | local | mEFCT_PWRON_CFOOF | 17 | #define mEFCT_PWRON_CFOOF 43 // Achtung! This is the awesome FOOF Rubber Band Gun.
PowerOn | 44 | 0044__mdo47__FOOF.wav | eSpeak mdo47 recording of "This is the awesome FOOF Rubber Band Gun. Be afraid." | PowerOn | Feel free to use the generated audio for any of your projects (commercial or personal). | LingoJam.com | https://lingojam.com/RobotVoiceGenerator | mEFCT_PWRON_RFOOF | 17 | #define mEFCT_PWRON_RFOOF 44 // This is the awesome FOOF Rubber Band Gun. Be afraid.
waiting | 51 | 240297__jalastram__abstract-guitar-sfx-003.wav | very cool science fictiony steady state | waiting | by/3.0/ | jalastram | https://freesound.org/s/240297/
waiting | 52 | 383760__deleted-user-7146007__laboratory-mad-scientist-science-fiction-sci-fi.wav | very nice steady state sound - science fictiony | waiting | zero/1.0/ | deleted-user-7146007 | https://freesound.org/s/383760/
waiting | 53 | 170136__lazr2012__machinery-bo.flac | very nice slow wow-wow - different tones - mostly bass | waiting | zero/1.0/ | lazr2012 | https://freesound.org/s/170136/
waiting | 54 | 500418__dj-somar__intro-reverso-craver-microbrute.wav | good steady - need to cut out the end (decrescendo) | waiting | zero/1.0/ | DJ_SoMaR | https://freesound.org/s/500418/
waiting | 55 | 169292__lazr2012__haywirefusionator.ogg | mucho machino - lots of sounds, could use for steady | waiting | by/3.0/ | lazr2012 | https://freesound.org/s/169292/
waiting | 56 | 88635__uair01__bicycle-picture-in-spectrum.wav | split for windup, waiting | windup waiting | by/3.0/ | uair01 | https://freesound.org/s/88635/
waiting | 57 | 417131__cuddlenucks__science-fiction-noise-3.wav | very nice straight decrescendo with blat at the end - maybe use for steady state | waiting | by/3.0/ | cuddlenucks | https://freesound.org/s/417131/
waiting | 58 | 221875__hero-of-the-winds__spring-boing.wav | different take on boing - could use steady state - use loud part at end | waiting | by/3.0/ | hero-of-the-winds | https://freesound.org/s/221875/ |  | 32 | maximum length of below
waiting | 59 | SKR-03-324.wav | Cassini sounds of Saturn radio waves. Needed to resample to standard bitrate to make this work | waiting | N/A | NASA Cassini University of Iowa | http://www-pw.physics.uiowa.edu/space-audio/cassini/SKR1/SKR-03-324.wav
unique | 62 | 0062__mdo47__cfg_introToConfig.wav | mdo47 recording of "Welcome to the FOOF Rubber Band Gun configuration! Your call is important to us. Press trigger by itself to go forward to next step or to cycle through choices. To select a choice, first hold down any combination of Yellow or Red button then press trigger. To exit configuration, hold down Green button then press trigger." | unique | by/3.0/ | mdo47 | local | mEFCT_UNIQ_INTRO | 16 | #define mEFCT_UNIQ_INTRO 62 // Welcome to the FOOF Rubber Band Gun configuration! Your call is important to us. Press trigger by itself to go forward to next step or to cycle through choices. To select a choice, first hold down any combination of Yellow or Red button then press trigger. To exit configuration, hold down Green button then press trigger.
unique | 63 | 0063__mdo47__cfg_configCategInstruct.wav | mdo47 recording of "Now choose which configuration category: sound effects, LED pattern effects, configuration resets and copying, or advanced settings. As always, press trigger by itself to go forward to next step or to cycle through choices. To select a choice, first hold down any combination of Yellow or Red button then press trigger. To exit configuration, hold down Green button then press trigger." | unique | by/3.0/ | mdo47 | local | mEFCT_UNIQ_CFG_CATEGORY | 23 | #define mEFCT_UNIQ_CFG_CATEGORY 63 // Now choose which configuration category: sound effects, LED pattern effects, configuration resets and copying, or advanced settings. As always, press trigger by itself to go forward to next step or to cycle through choices. To select a choice, first hold down any combination of Yellow or Red button then press trigger. To exit configuration, hold down Green button then press trigger.
unique | 64 | 0064__mdo47__cfg_configWhenInstruct.wav | mdo47 recording of "Now choose when the effect happens. This list includes when powering-on, when shooting, etc. As always, press trigger by itself to go forward to next step or to cycle through choices. To select a choice, first hold down any combination of Yellow or Red button then press trigger. To exit configuration, hold down Green button then press trigger." | unique | by/3.0/ | mdo47 | local | mEFCT_UNIQ_CFG_TYPE | 19 | #define mEFCT_UNIQ_CFG_TYPE 64 // Now choose when the effect happens. This list includes when powering-on, when shooting, etc. As always, press trigger by itself to go forward to next step or to cycle through choices. To select a choice, first hold down any combination of Yellow or Red button then press trigger. To exit configuration, hold down Green button then press trigger.
unique | 65 | 0065__mdo47__cfg_configEffectInstruct.wav | mdo47 recording of "Now choose the effect itself. This list cycles through the effects one by one. As always, press trigger by itself to go forward to next step or to cycle through choices. To select a choice, first hold down any combination of Yellow or Red button then press trigger. To exit configuration, hold down Green button then press trigger." | unique | by/3.0/ | mdo47 | local | mEFCT_UNIQ_CFG_EFFECT | 21 | #define mEFCT_UNIQ_CFG_EFFECT 65 // Now choose the effect itself. This list cycles through the effects one by one. As always, press trigger by itself to go forward to next step or to cycle through choices. To select a choice, first hold down any combination of Yellow or Red button then press trigger. To exit configuration, hold down Green button then press trigger.
unique | 66 | 0066__mdo47__cfg_LED2choose.wav | mdo47 recording of "This is an LED pattern you can choose. As always, press trigger by itself to go forward to next step or to cycle through choices. To select a choice, first hold down any combination of Yellow or Red button then press trigger. To exit configuration, hold down Green button then press trigger." | unique | by/3.0/ | mdo47 | local | mEFCT_UNIQ_CFG_LED2CHOOSE | 25 | #define mEFCT_UNIQ_CFG_LED2CHOOSE 66 // This is an LED pattern you can choose. As always, press trigger by itself to go forward to next step or to cycle through choices. To select a choice, first hold down any combination of Yellow or Red button then press trigger. To exit configuration, hold down Green button then press trigger.
unique | 67 | 0067__mdo47__cfg_configAccepted.wav | mdo47 recording of "Your choice has been saved into the running settings." | unique | by/3.0/ | mdo47 | local | mEFCT_UNIQ_CFG_ACCEPT | 21 | #define mEFCT_UNIQ_CFG_ACCEPT 67 // Your choice has been saved into the running settings.
unique | 68 | 0068__mdo47__uniqSorryNotYetImplemented.wav | mdo47 recording of "This feature is not yet implemented." | unique | by/3.0/ | mdo47 | local | mEFCT_UNIQ_NOT_IMPL | 19 | #define mEFCT_UNIQ_NOT_IMPL 68 // This feature is not yet implemented.
unique | 69 | 0069__mdo47__silence.wav | mdo47 recording of "silence" | unique | by/3.0/ | mdo47 | local | mEFCT_UNIQ_SILENCE | 18 | #define mEFCT_UNIQ_SILENCE 69 // silence
unique | 71 | 0071__mdo47__cfg_efct_windup_descrip.wav | mdo47 recording of "The effect happens during wind-up to shooting." | unique | by/3.0/ | mdo47 | local | mEFCT_UNIQ_CFG_WINDUP_DESCRIP | 29 | #define mEFCT_UNIQ_CFG_WINDUP_DESCRIP 71 // The effect happens during wind-up to shooting.
unique | 72 | 0072__mdo47__cfg_efct_shoot_descrip.wav | mdo47 recording of "The effect happens during shooting itself." | unique | by/3.0/ | mdo47 | local | mEFCT_UNIQ_CFG_SHOOT_DESCRIP | 28 | #define mEFCT_UNIQ_CFG_SHOOT_DESCRIP 72 // The effect happens during shooting itself.
unique | 73 | 0073__mdo47__cfg_efct_open_descrip.wav | mdo47 recording of "The effect happens during opening of the barrel." | unique | by/3.0/ | mdo47 | local | mEFCT_UNIQ_CFG_OPEN_DESCRIP | 27 | #define mEFCT_UNIQ_CFG_OPEN_DESCRIP 73 // The effect happens during opening of the barrel.
unique | 74 | 0074__mdo47__cfg_efct_loklod_descrip.wav | mdo47 recording of "The effect happens during lock-and-load of the barrel." | unique | by/3.0/ | mdo47 | local | mEFCT_UNIQ_CFG_LKLOD_DESCRIP | 28 | #define mEFCT_UNIQ_CFG_LKLOD_DESCRIP 74 // The effect happens during lock-and-load of the barrel.
unique | 75 | 0075__mdo47__cfg_efct_pwron_descrip.wav | mdo47 recording of "The effect happens during initial power-on." | unique | by/3.0/ | mdo47 | local | mEFCT_UNIQ_CFG_PWRON_DESCRIP | 28 | #define mEFCT_UNIQ_CFG_PWRON_DESCRIP 75 // The effect happens during initial power-on.
unique | 76 | 0076__mdo47__cfg_efct_wait_descrip.wav | mdo47 recording of "The effect happens when waiting to shoot." | unique | by/3.0/ | mdo47 | local | mEFCT_UNIQ_CFG_WAIT_DESCRIP | 27 | #define mEFCT_UNIQ_CFG_WAIT_DESCRIP 76 // The effect happens when waiting to shoot.
unique | 81 | 0081__mdo47__cfg_efct_sounds.wav | mdo47 recording of "The category is SOUNDS." | unique | by/3.0/ | mdo47 | local | mEFCT_UNIQ_CFG_SOUNDS_DESCRIP | 29 | #define mEFCT_UNIQ_CFG_SOUNDS_DESCRIP 81 // The category is SOUNDS.
unique | 82 | 0082__mdo47__cfg_efct_led_patterns.wav | mdo47 recording of "The category is L. E. D. PATTERNS." | unique | by/3.0/ | mdo47 | local | mEFCT_UNIQ_CFG_LEDPTRN_DESCRIP | 30 | #define mEFCT_UNIQ_CFG_LEDPTRN_DESCRIP 82 // The category is L. E. D. PATTERNS.
unique | 83 | 0083__mdo47__cfg_categ_copy_reset.wav | mdo47 recording of "The category is configuration resets and copying." | unique | by/3.0/ | mdo47 | local | mEFCT_UNIQ_CFG_CPY_RST_DESCRIP | 30 | #define mEFCT_UNIQ_CFG_CPY_RST_DESCRIP 83 // The category is configuration resets and copying.
unique | 84 | 0084__mdo47__cfg_categ_advanced_settings.wav | mdo47 recording of "The category is advanced settings." | unique | by/3.0/ | mdo47 | local | mEFCT_UNIQ_CFG_ADVANCED_DESCRIP | 31 | #define mEFCT_UNIQ_CFG_ADVANCED_DESCRIP 84 // The category is advanced settings.
unique | 86 | 0086__mdo47__cfg_enter_password.wav | mdo47 recording of "Please state password loudly, then press trigger." | unique | by/3.0/ | mdo47 | local | mEFCT_UNIQ_CFG_ENTER_PASSWORD | 29 | #define mEFCT_UNIQ_CFG_ENTER_PASSWORD 86 // Please state password loudly, then press trigger.
unique | 87 | 0087__mdo47__cfg_enter_dance.wav | mdo47 recording of "I could not understand your password, please enter password by interpretive dance, then press trigger." | unique | by/3.0/ | mdo47 | local | mEFCT_UNIQ_CFG_ENTER_DANCE | 26 | #define mEFCT_UNIQ_CFG_ENTER_DANCE 87 // I could not understand your password, please enter password by interpretive dance, then press trigger.
unique | 88 | 0088__mdo47__cfg_sorry_no_password.wav | mdo47 recording of "Sorry, I don't have a password, but you dance very well. Please press trigger." | unique | by/3.0/ | mdo47 | local | mEFCT_UNIQ_CFG_SORRY_NO_PASSWORD | 32 | #define mEFCT_UNIQ_CFG_SORRY_NO_PASSWORD 88 // Sorry, I don't have a password, but you dance very well. Please press trigger.
unique | 89 | 0089__mdo47__cfg__credits.wav | mdo47 recording of "The FOOF Science Fiction Rubber Band Gun was originally conceived by Mark and Keith. The hardware implementation was designed and built by Jim. The software and most of the sounds were generated by Mark. Some build information is at Git Hub dot Com slash Mark Dash Em Dee Oh Forty Seven dot Com slash Rubber Band Gun. Some sounds are recordings of Mark's family. Many of the Sci Fi sounds are transmogrified versions of Creative Commons sounds stored on Free Sound dot Org. Other Sci Fi sounds originated from El Eye Gee Oh gravity wave detections of stellar events found at Gee Double You Dash Open Science dot Org slash Audio Gee Double You Tee See One. The robotic voice sounds were generated using the eSpeak text to speech program found on eSpeak dot Source Forge dot net. See the Git Hub page for more attributions." | unique | by/3.0/ | mdo47 | local | mEFCT_UNIQ_CFG_CREDITS | 22 | #define mEFCT_UNIQ_CFG_CREDITS 89 // The FOOF Science Fiction Rubber Band Gun was originally conceived by Mark and Keith. The hardware implementation was designed and built by Jim. The software and most of the sounds were generated by Mark. Some build information is at Git Hub dot Com slash Mark Dash Em Dee Oh Forty Seven dot Com slash Rubber Band Gun. Some sounds are recordings of Mark's family. Many of the Sci Fi sounds are transmogrified versions of Creative Commons sounds stored on Free Sound dot Org. Other Sci Fi sounds originated from El Eye Gee Oh gravity wave detections of stellar events found at Gee Double You Dash Open Science dot Org slash Audio Gee Double You Tee See One. The robotic voice sounds were generated using the eSpeak text to speech program found on eSpeak dot Source Forge dot net. See the Git Hub page for more attributions.
unique | 91 | 0091__mdo47__cfg_mgmt_01.wav | mdo47 recording of "Erase the running setting only and reset the running setting to the factory settings." | unique | by/3.0/ | mdo47 | local | mEFCT_UNIQ_CFG_MGMT_01 | 22 | #define mEFCT_UNIQ_CFG_MGMT_01 91 // Erase the running setting only and reset the running setting to the factory settings.
unique | 92 | 0092__mdo47__cfg_mgmt_02.wav | mdo47 recording of "Erase the running setting and erase all saved auxilliary settings and reset to the factory settings." | unique | by/3.0/ | mdo47 | local | mEFCT_UNIQ_CFG_MGMT_02 | 22 | #define mEFCT_UNIQ_CFG_MGMT_02 92 // Erase the running setting and erase all saved auxilliary settings and reset to the factory settings.
unique | 93 | 0093__mdo47__cfg_mgmt_03.wav | mdo47 recording of "Copy the running setting and overwrite into saved auxilliary setting number one." | unique | by/3.0/ | mdo47 | local | mEFCT_UNIQ_CFG_MGMT_03 | 22 | #define mEFCT_UNIQ_CFG_MGMT_03 93 // Copy the running setting and overwrite into saved auxilliary setting number one.
unique | 94 | 0094__mdo47__cfg_mgmt_04.wav | mdo47 recording of "Copy the running setting and overwrite into saved auxilliary setting number two." | unique | by/3.0/ | mdo47 | local | mEFCT_UNIQ_CFG_MGMT_04 | 22 | #define mEFCT_UNIQ_CFG_MGMT_04 94 // Copy the running setting and overwrite into saved auxilliary setting number two.
unique | 95 | 0095__mdo47__cfg_mgmt_05.wav | mdo47 recording of "Copy the running setting and overwrite into saved auxilliary setting number three." | unique | by/3.0/ | mdo47 | local | mEFCT_UNIQ_CFG_MGMT_05 | 22 | #define mEFCT_UNIQ_CFG_MGMT_05 95 // Copy the running setting and overwrite into saved auxilliary setting number three.
unique | 96 | 0096__mdo47__cfg_mgmt_06.wav | mdo47 recording of "Copy the saved auxilliary setting number one and overwrite into the running setting." | unique | by/3.0/ | mdo47 | local | mEFCT_UNIQ_CFG_MGMT_06 | 22 | #define mEFCT_UNIQ_CFG_MGMT_06 96 // Copy the saved auxilliary setting number one and overwrite into the running setting.
unique | 97 | 0097__mdo47__cfg_mgmt_07.wav | mdo47 recording of "Copy the saved auxilliary setting number two and overwrite into the running setting." | unique | by/3.0/ | mdo47 | local | mEFCT_UNIQ_CFG_MGMT_07 | 22 | #define mEFCT_UNIQ_CFG_MGMT_07 97 // Copy the saved auxilliary setting number two and overwrite into the running setting.
unique | 98 | 0098__mdo47__cfg_mgmt_08.wav | mdo47 recording of "Copy the saved auxilliary setting number three and overwrite into the running setting." | unique | by/3.0/ | mdo47 | local | mEFCT_UNIQ_CFG_MGMT_08 | 22 | #define mEFCT_UNIQ_CFG_MGMT_08 98 // Copy the saved auxilliary setting number three and overwrite into the running setting.
unique | 101 | 0101__mdo47__cfg_advanced_01.wav | mdo47 recording of "Static mode: Repeat the running settings effects each time you shoot. Power cycle to exit Static mode and return to Dynamic mode. As always, press trigger by itself to go forward to next step or to cycle through choices. To select a choice, first hold down any combination of Yellow or Red button then press trigger. To exit configuration, hold down Green button then press trigger." | unique | by/3.0/ | mdo47 | local | mEFCT_UNIQ_CFG_ADVANCED_01 | 26 | #define mEFCT_UNIQ_CFG_ADVANCED_01 101 // Static mode: Repeat the running settings effects each time you shoot. Power cycle to exit Static mode and return to Dynamic mode. As always, press trigger by itself to go forward to next step or to cycle through choices. To select a choice, first hold down any combination of Yellow or Red button then press trigger. To exit configuration, hold down Green button then press trigger.
unique | 102 | 0102__mdo47__cfg_advanced_02.wav | mdo47 recording of "Enable time travel and teleportation capabilities (requires password). As always, press trigger by itself to go forward to next step or to cycle through choices. To select a choice, first hold down any combination of Yellow or Red button then press trigger. To exit configuration, hold down Green button then press trigger." | unique | by/3.0/ | mdo47 | local | mEFCT_UNIQ_CFG_ADVANCED_02 | 26 | #define mEFCT_UNIQ_CFG_ADVANCED_02 102 // Enable time travel and teleportation capabilities (requires password). As always, press trigger by itself to go forward to next step or to cycle through choices. To select a choice, first hold down any combination of Yellow or Red button then press trigger. To exit configuration, hold down Green button then press trigger.
unique | 103 | 0103__mdo47__cfg_advanced_03.wav | mdo47 recording of "Hear Rubber Band Gun credits. As always, press trigger by itself to go forward to next step or to cycle through choices. To select a choice, first hold down any combination of Yellow or Red button then press trigger. To exit configuration, hold down Green button then press trigger." | unique | by/3.0/ | mdo47 | local | mEFCT_UNIQ_CFG_ADVANCED_03 | 26 | #define mEFCT_UNIQ_CFG_ADVANCED_03 103 // Hear Rubber Band Gun credits. As always, press trigger by itself to go forward to next step or to cycle through choices. To select a choice, first hold down any combination of Yellow or Red button then press trigger. To exit configuration, hold down Green button then press trigger.
unique | 104 | 0104__mdo47__shoot_unused.wav | mdo47 recording of "Unused Sound File." | unique | by/3.0/ | mdo47 | local | mEFCT_UNIQ_SHOOT_UNUSED | 23 | #define mEFCT_UNIQ_SHOOT_UNUSED 104 // Unused Sound File.
unique | 105 | 0105__mdo47__shoot_too_soon.wav | mdo47 recording of "Sorry, too soon to shoot rubber band again." | unique | by/3.0/ | mdo47 | local | mEFCT_UNIQ_SHOOT_TOO_SOON | 25 | #define mEFCT_UNIQ_SHOOT_TOO_SOON 105 // Sorry, too soon to shoot rubber band again.
unique | 106 | 0106__mdo47__cfg_advanced.wav | mdo47 recording of "Now choose which ADVANCED configuration category: Static Effect Mode, Time Travel and Teleportation, or Credits. As always, press trigger by itself to go forward to next step or to cycle through choices. To select a choice, first hold down any combination of Yellow or Red button then press trigger. To exit configuration, hold down Green button then press trigger." | unique | by/3.0/ | mdo47 | local | mEFCT_UNIQ_CFG_ADVANCED | 23 | #define mEFCT_UNIQ_CFG_ADVANCED 106 // Now choose which ADVANCED configuration category: Static Effect Mode, Time Travel and Teleportation, or Credits. As always, press trigger by itself to go forward to next step or to cycle through choices. To select a choice, first hold down any combination of Yellow or Red button then press trigger. To exit configuration, hold down Green button then press trigger.
unique | 107 | 0107__mdo47__cfg_static_started.wav | mdo47 recording of "Static mode started. Power cycle to exit Static mode." | unique | by/3.0/ | mdo47 | local | mEFCT_UNIQ_CFG_STATIC_STARTED | 29 | #define mEFCT_UNIQ_CFG_STATIC_STARTED 107 // Static mode started. Power cycle to exit Static mode.
unique | 108 | 0108__mdo47__cfg_cpy_rst_intro.wav | mdo47 recording of "Now choose the, factory reset, or, configuration, copy, option. This list cycles through the options one by one. As always, press trigger by itself to go forward to next step or to cycle through choices. To select a choice, first hold down any combination of Yellow or Red button then press trigger. To exit configuration, hold down Green button then press trigger." | unique | by/3.0/ | mdo47 | local | mEFCT_UNIQ_CFG_CPY_RST | 22 | #define mEFCT_UNIQ_CFG_CPY_RST 108 // Now choose the, factory reset, or, configuration, copy, option. This list cycles through the options one by one. As always, press trigger by itself to go forward to next step or to cycle through choices. To select a choice, first hold down any combination of Yellow or Red button then press trigger. To exit configuration, hold down Green button then press trigger.
unique | 109 | 0109__mdo47__cfg_cpy_rst_accept.wav | mdo47 recording of "Your, factory reset, or, configuration copy, option, has been accepted. Rebooting." | unique | by/3.0/ | mdo47 | local | mEFCT_UNIQ_CFG_CPY_RST_ACCEPT | 29 | #define mEFCT_UNIQ_CFG_CPY_RST_ACCEPT 109 // Your, factory reset, or, configuration copy, option, has been accepted. Rebooting.
END | END | END | END | END | END | END | END | END
 |  |  |  |  |  |  |  |  |  | #define mEFCT_WIND_UP 0 // 001 to 009 - wind-up effects
 |  |  |  |  |  |  |  |  |  | #define mEFCT_SHOOT 10 // 011 to 019 - shoot effects
 |  |  |  |  |  |  |  |  |  | #define mEFCT_OPEN_BARREL 20 // 021 to 029 - open barrel effects
 |  |  |  |  |  |  |  |  |  | #define mEFCT_LOCK_LOAD 30 // 031 to 039 - lock and load barrel effects
 |  |  |  |  |  |  |  |  |  | #define mEFCT_PWRON 40 // 041 to 049 - initial power-up effects
 |  |  |  |  |  |  |  |  |  | #define mEFCT_WAIT 50 // 051 to 059 - waiting for trigger |  |  | | Tag | File Name | URL | Who
 |  |  |  |  |  |  |  |  |  | #define mEFCT_CONFIGURE 60 // 061 to 099 - effects used to navigate menus |  |  | | --- | --- | --- | ---
 |  |  |  |  |  |  |  |  |  | #define mEFCT_UNIQ 100 // 101 to 127 - unique effects not included in configurations |  |  | | zero/1.0/ | 407052__sojan__power-charge.flac | https://freesound.org/s/193610/ | crashoverride61088
windup |  | 179281__timbre__boingy-sweep.flac | heavily used in windup mashup | windup | by-nc/3.0/ | Timbre | https://freesound.org/s/179281/
windup |  | 216096__richerlandtv__u-f-o.mp3 | heavily used in windup mashup | windup | by/3.0/ | RICHERlandTV | https://freesound.org/s/216096/
waiting | 57 | 162814__timgormly__spaceship-4.aiff | steady state science fictiony not much variation - high pitch | waiting | zero/1.0/ | timgormly | https://freesound.org/s/162814/
waiting | 58 | 165483__timbre__glitch-voice-ep-mp3.mp3 | very busy, lot of glitches, hard to see use for us | waiting | by-nc/3.0/ | timbre | https://freesound.org/s/165483/
<html><body>
Note: sounds on this card have a naming convention to optimize use with the YX5200 module. These names do not correspond directly to the filenames listed below, which are the source file names.<br>
Attribution of sounds found (in whole or in part, possibly altered) on this SD card:<br><br>
<table border cellspacing="1" cellpadding="9">
<tr><td><b>Tag</b></td><td><b>File Name</b></td><td><b>URL</b></td><td><b>Who</b></td> |  |  |  |  |  |  |  |  | Tag | File Name | URL | Who
<tr><td>N/A</td><td>GW170817-template.wav</td><td>https://www.gw-openscience.org/audiogwtc1/</td><td>LIGO detectors</td> |  |  |  |  |  |  |  |  | N/A | GW170817-template.wav | https://www.gw-openscience.org/audiogwtc1/ | LIGO detectors
<tr><td>zero/1.0/</td><td>145209__lensflare8642__shotgun-sounds.mp3</td><td>https://freesound.org/s/145209/</td><td>lensflare8642</td> |  |  |  |  |  |  |  |  | zero/1.0/ | 145209__lensflare8642__shotgun-sounds.mp3 | https://freesound.org/s/145209/ | lensflare8642 | | zero/1.0/ | 145209__lensflare8642__shotgun-sounds.mp3 | https://freesound.org/s/145209/ | lensflare8642
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

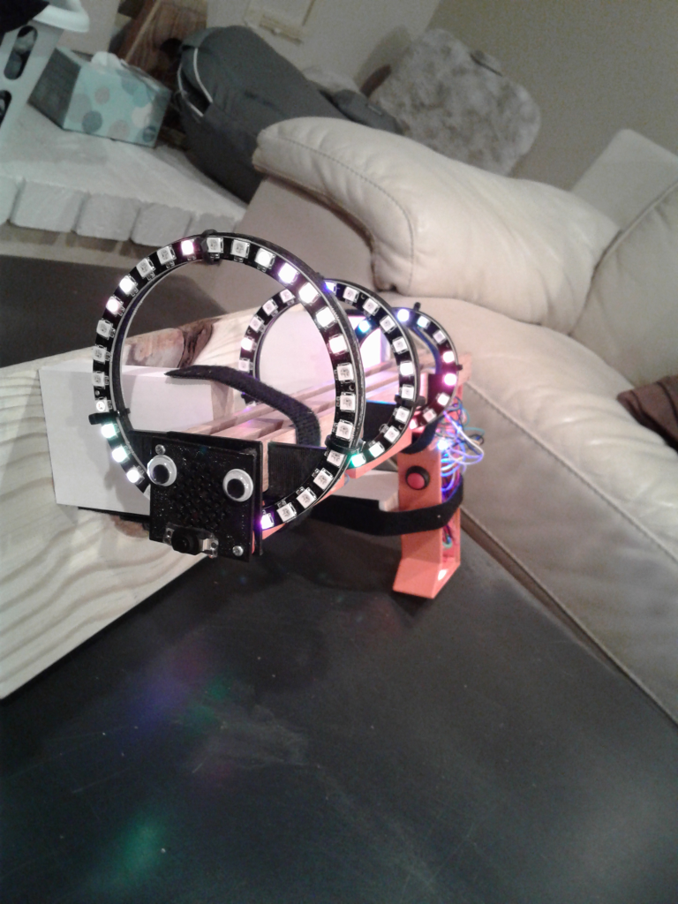
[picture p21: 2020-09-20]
PartsInfo/RBG_googly_eyes_20200919_210308.png

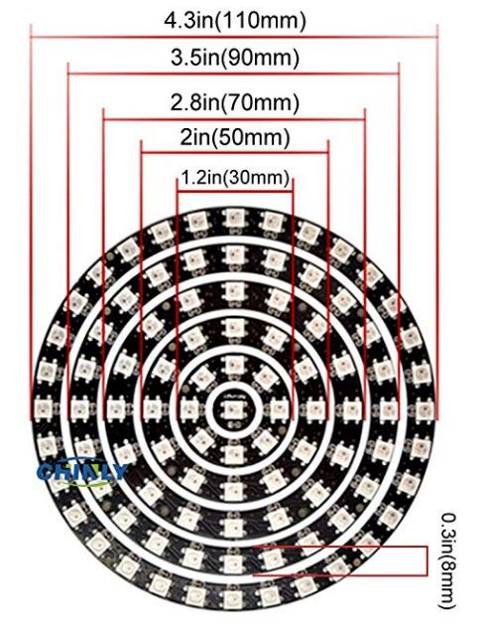
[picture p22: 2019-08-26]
PartsInfo/LED_Dimensions.png

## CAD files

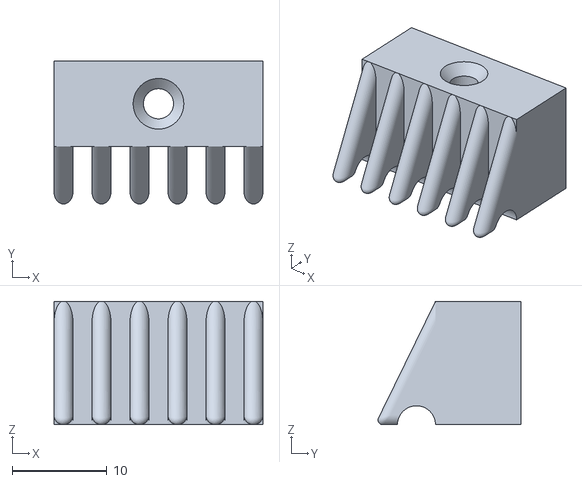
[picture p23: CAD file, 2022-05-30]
3D_model/barrel end rubber band holder v1.stl
22.0 x 15.0 x 13.0

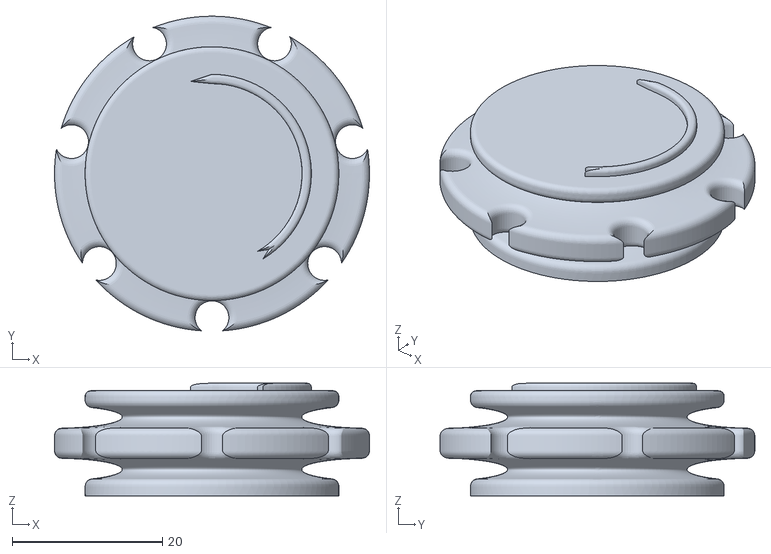
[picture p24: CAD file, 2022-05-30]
3D_model/Rotor.stl
42.0 x 42.0 x 15.0

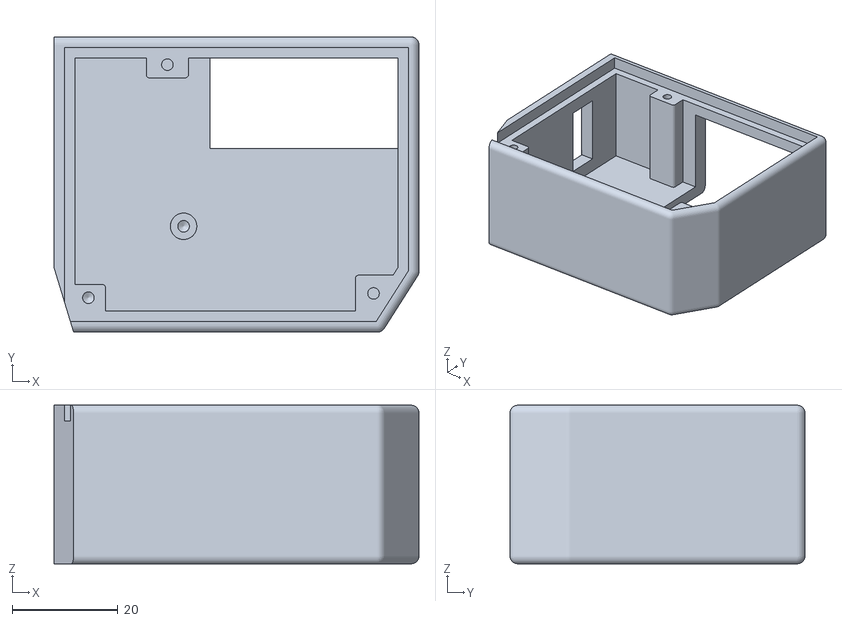
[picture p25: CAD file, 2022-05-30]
3D_model/Sidewinder Motor housing.stl
69.0 x 55.8 x 30.0

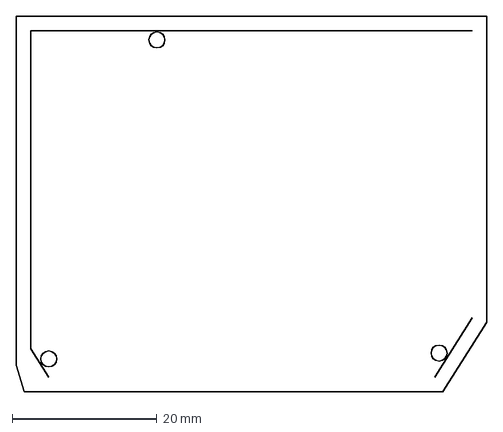
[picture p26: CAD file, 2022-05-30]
3D_model/sidewinder housing cover.dxf
65.0 x 51.8 mm

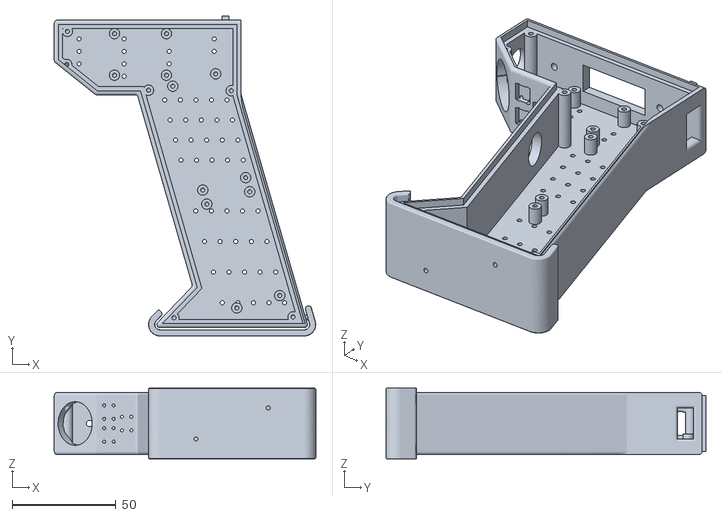
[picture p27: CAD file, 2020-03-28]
3D_model/RBG body 4.stl
125.9 x 154.0 x 34.0

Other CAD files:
3D_model/RBG body 4.f3d
3D_model/clothespin holder.f3d
3D_model/single battery holder and lid 5.f3d

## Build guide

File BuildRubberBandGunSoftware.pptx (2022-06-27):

## Build FOOF Rubber Band Gun SW https://github.com/Mark-MDO47/RubberBandGun

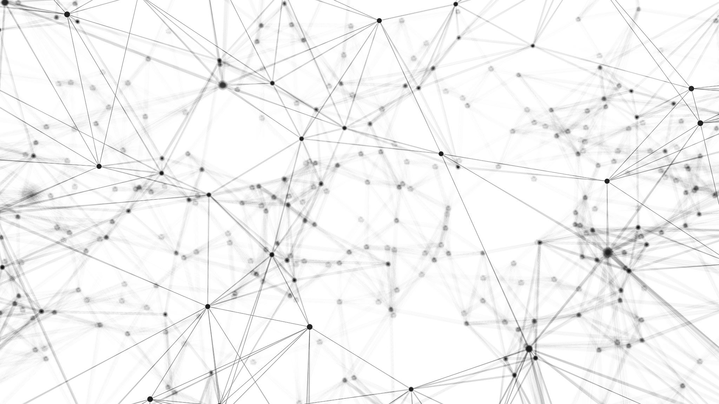
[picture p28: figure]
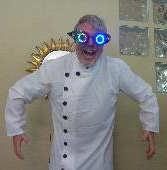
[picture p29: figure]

… the AWESOME

24 June 2022

## FOOF Rubber Band Gun Operation

Done

Trig
Only

Config

Trig
+ Green

Trig
+ Green

Shoot

Sound
Or
LED

When
What
Choose

Trig
+ R/Y

Pwr
On

This is the
FOOF RBG…

Wait

Trig
+ R/Y

Trig
+ Green

Cfg
Reset
Copy

Trig
+ Green

Fctry Rst
Copy

Do
It

Trig
+ R/Y

Trig
+ R/Y

Trig
+ R/Y

Advanced

Trig
+ Green

Trig
+ R/Y

Demo
Time
Credits

Trig
+ R/Y

Trig
+ Green

Trig
+ Green

## FOOF Rubber Band Gun State Machine and Factory Settings

Tab ‘StateTable’
In Spreadsheet

makeStateTable.py

State Table Code

Excel ™

editor

RBG_SciFi_StatesAndInputs.h

Tab ‘Rules’ in Spreadsheet

Annotated
Tab ‘StateTable’
In Spreadsheet

Tab ‘Sounds’
In Spreadsheet

Excel ™

Tab ‘FactorySettings’
In Spreadsheet

editor

RBG_SciFi_StatesAndInputs.h

Tab ‘LEDpatterns’
In Spreadsheet

## FOOF Rubber Band Gun eSpeak and Sound Files

bash.exe and eSpeak

Reformat
SD Card

Tab ‘Sounds’
In Spreadsheet

RobotSounds.py

eSpeak script

copyem.py

*.wav Files

Audacity

raw_*.wav Files

docopyem script

bash.exe

Insert SD Card
in YX5200

## FOOF Rubber Band Gun Debug Tools

RBG_SciFi_StatesAndInputs.h
RBG_SciFi.ino

VS_debuggable.py

*.cpp code

Visual Studio 2019
Console App

Debug State Transitions

Run RBG with Debug Options

Copy “COM” output
To debug2.txt

Tab ‘debugging’
In Spreadsheet
“grep” statements

bash.exe

Tab ‘debugging’
In Spreadsheet

Sort,
Remove dups,
Debug

## FOOF Rubber Band Gun RBG_SciFi.ino Arduino Setup

- Board “Arduino Nano”
- Processor “ATmega328P (Old Bootloader)”
- Programmer “AVRISP mkll”

https://support.arduino.cc/hc/en-us/articles/360016785580-Error-avrdude-stk500-getsync-attempt-X-of-10-not-in-sync-resp-
Error: avrdude: stk500_getsync() attempt X of 10: not in sync: resp=

1. If your Arduino NANO was purchased earlier than 2018 you have the older official version of Nano. In this case Select Tools > Processor > ATmega328P and select: (Old Bootloader) and try to compile your sketch again. It is also recommended to update Arduino AVR Core 1.16.21 or later through Boards Manager.
2. If you have the newer version of the Nano board (manufactured in 2018 or later), make sure you have Arduino AVR Boards 1.6.21 or newer installed. Check this in Arduino IDE: Tools > Board > Boards Manager and select Tools > Processor > ATmega328P.

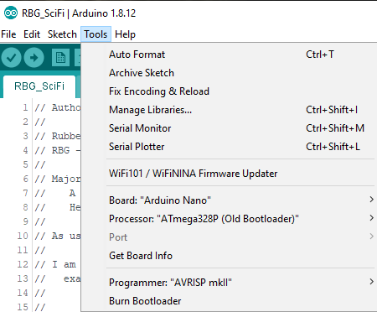
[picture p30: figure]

## FOOF Rubber Band Gun RBG_SciFi.ino programming

RBG_SciFi.ino
Take the clear acrylic cover off, pull back the barrel/solenoid/motor assembly as if loading, turn the RBG power on, plug in the USB Male Mini 5 Pin to the Arduino NANO and the other side to your computer, and program. Reverse steps to disconnect.
NOTE: when the RBG power is on while the USB connector is connected and periodically resetting the Arduino, it continuously resets and pulses the solenoid/motor circuit at an interval of about 1.5 seconds. This might eventually damage the solenoid/motor or its circuitry, so it is important to pull back the barrel/solenoid/motor assembly before powering on.
NOTE: The reason I suggest powering on the RBG while programming is so that the entire RBG is not being powered through our inexpensive clone Arduino Nano.

YX
5200

UBEC

125

IN

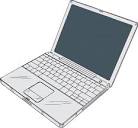
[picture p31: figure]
Image result for free clip art laptop

USB

KCX

Ardu

## FOOF Rubber Band Gun Programming Arduino for Bluetooth

YX
5200

Connections to program the KCX-BT-EMITTER
- See RubberBandGun_wiring.pdf
- See ProgrammingArduino_SerialMonitor_SampleOutput.pdf
- See ProgrammingArduino.ino

USB

UBEC

125

IN

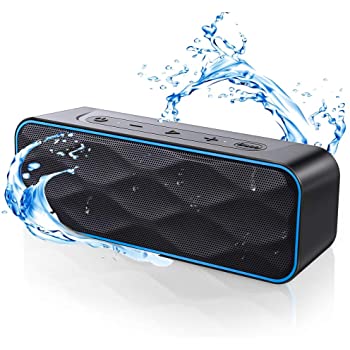
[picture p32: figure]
Bluetooth Speakers, ZoeeTree S1Pro Speaker Bluetooth Wireless with 20W HD Sound & Deep Bass, IPX7 Waterproof Speaker with 36Hours, 100Ft Wireless Range, Portable Speakers for Home, Outdoors, Travel

Prog Ardu

3 wires

KCX

Ardu

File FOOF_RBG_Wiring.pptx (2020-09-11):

## FOOF RBG Wiring https://github.com/Mark-MDO47/RubberBandGun


… the AWESOME


2020-09-10

## FOOF RBG Electronics Compartment

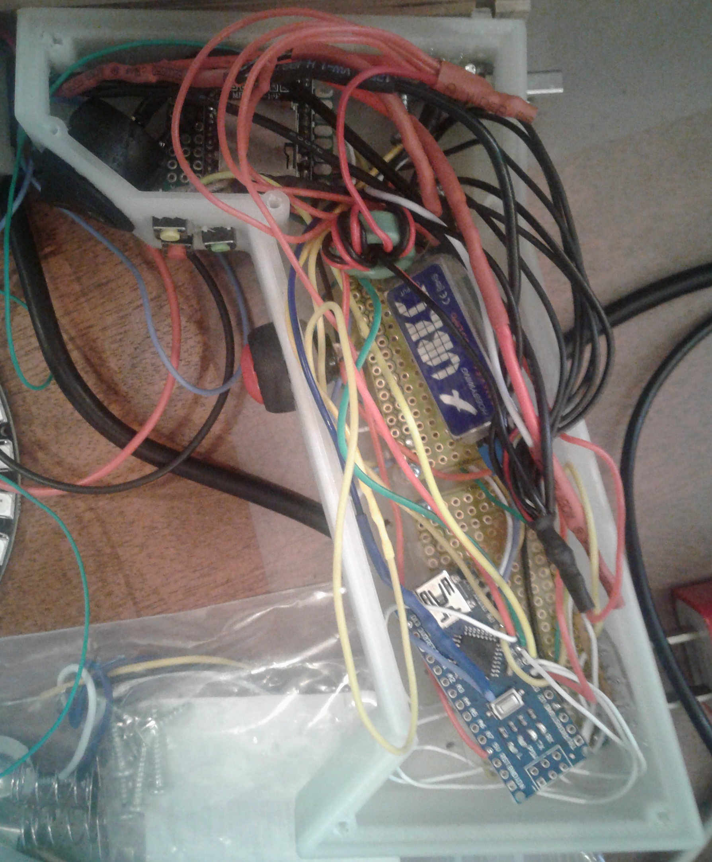
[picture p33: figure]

YX
5200

UBEC

125

KCX

IN

Ardu

## FOOF RBG Power

Battery 8.3V: 1 connection:
- on/off switch
USB 8.3V: 3 connections:
- on/off switch
- USB White Wire
- UBEC +V Input
LEDs 5V 20 AWG: 6 connections:
- YX5200 pin “01”
- Arduino pin “5V”
- UBEC 5V output
- SN74HCT125N pin “14”
- 10K Ohm SIP pin “??”
- KCX_BT_EMITTER pin “+5V”

LEDs 5V 20 AWG

Battery 8.3V

YX
5200

UBEC

125

KCX

USB 8.3V
White Wire

Ardu

IN

## FOOF RBG Ground

Note: UBEC grounds CONNECTED
LED GND 20 AWG : 8 connections:
- YX5200 pin “10”
- Arduino pin “GND”
- UBEC GND input
- UBEC GND output
- SN74HCT125N pin “07”
- USB Black Wire
- KCX_BT_EMITTER pin “GND”

LED GND 20 AWG

YX
5200

UBEC

125

KCX

IN

Ardu

## FOOF RBG USB Connector Other

YX
5200

UBEC

IN

125

KCX

Ardu

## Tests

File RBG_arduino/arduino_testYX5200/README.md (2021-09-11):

NOTE: this file is here for historical reasons. For using an Arduino to program the YX5200 module, use ProgrammingArduino here
https://github.com/Mark-MDO47/RubberBandGun/blob/master/RBG_arduino/ProgrammingArduino/ProgrammingArduino.ino

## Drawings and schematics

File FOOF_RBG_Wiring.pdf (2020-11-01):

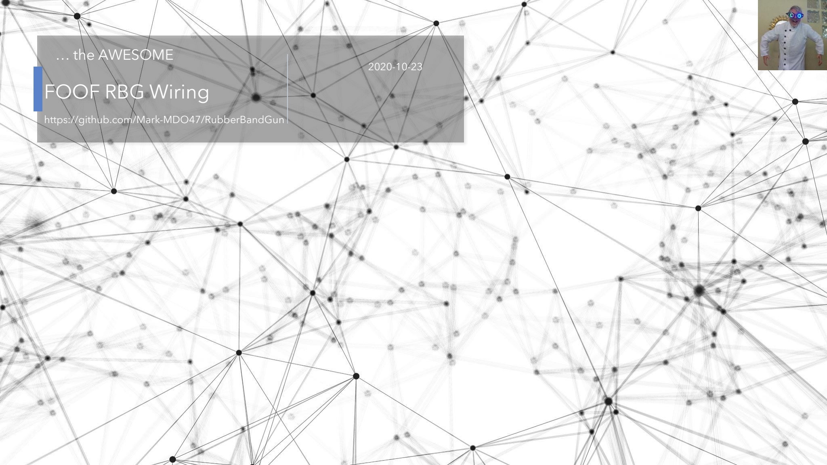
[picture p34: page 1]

FOOF RBG Wiring

https://github.com/Mark-MDO47/RubberBandGun

… the AWESOME
2020-10-23

# FOOF RBG Electronics Compartment125

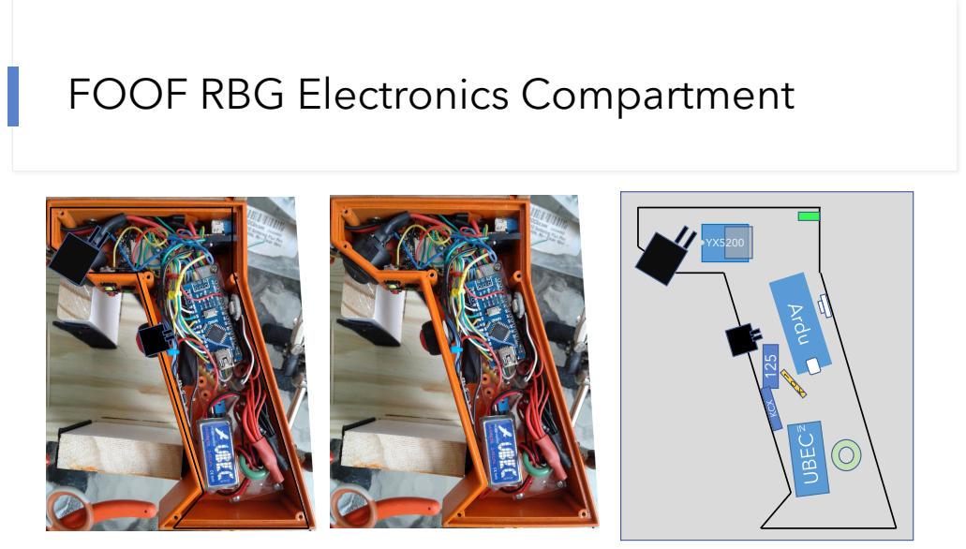
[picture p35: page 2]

# FOOF RBG 8.3V Power

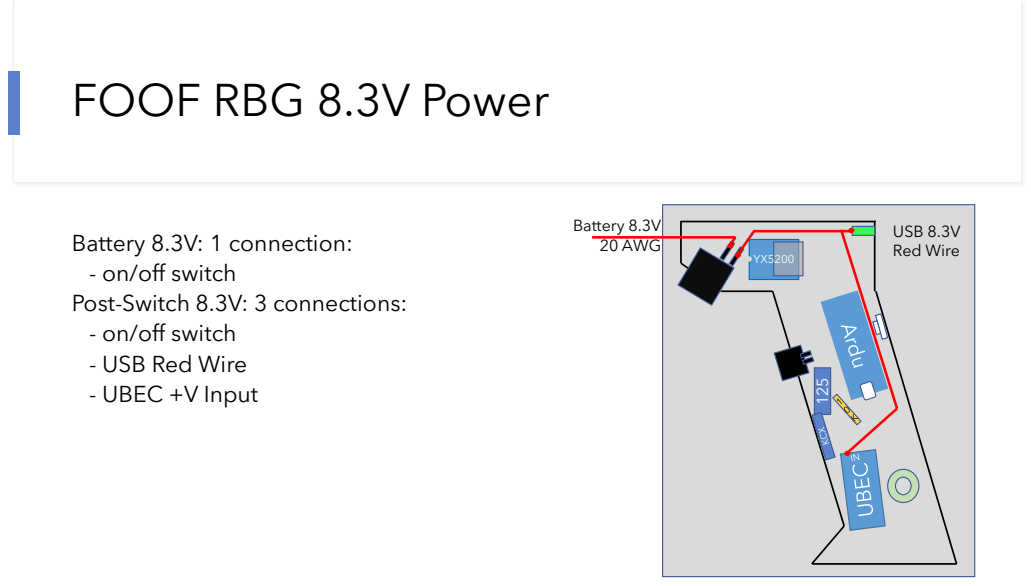
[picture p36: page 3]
USB 8.3V Red Wire; Battery 8.3V 20 AWG

Battery 8.3V: 1 connection:
- on/off switch
Post-Switch 8.3V: 3 connections:
- USB Red Wire
- UBEC +V Input

# FOOF RBG 5V Power

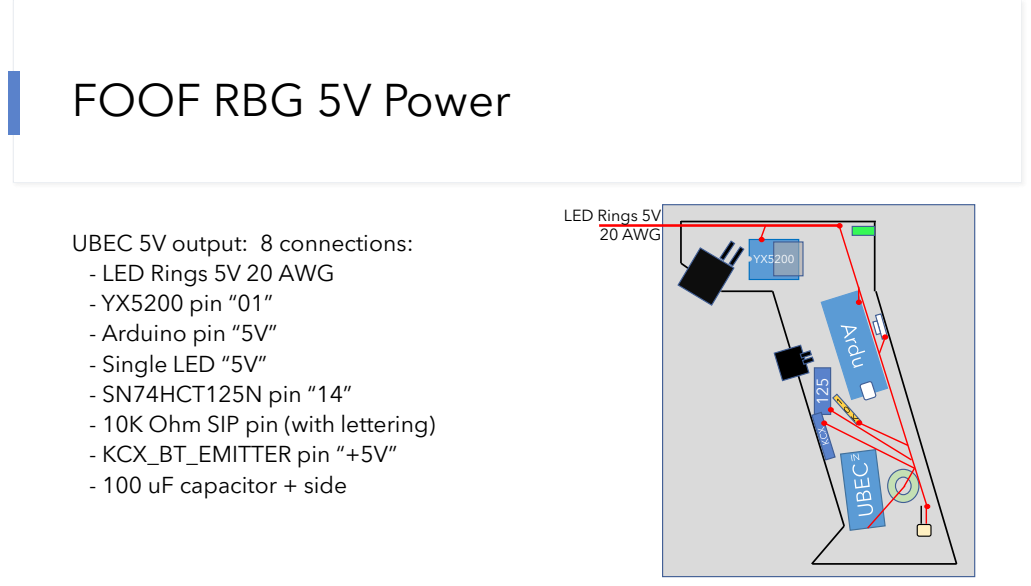
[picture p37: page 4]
LED Rings 5V 20 AWG

UBEC 5V output: 8 connections:
- LED Rings 5V 20 AWG
- YX5200 pin “01”
- Arduino pin “5V”
- Single LED “5V”
- SN74HCT125N pin “14”
- 10K Ohm SIP pin (with lettering)
- KCX_BT_EMITTER pin “+5V”
- 100 uF capacitor + side

# FOOF RBG Ground

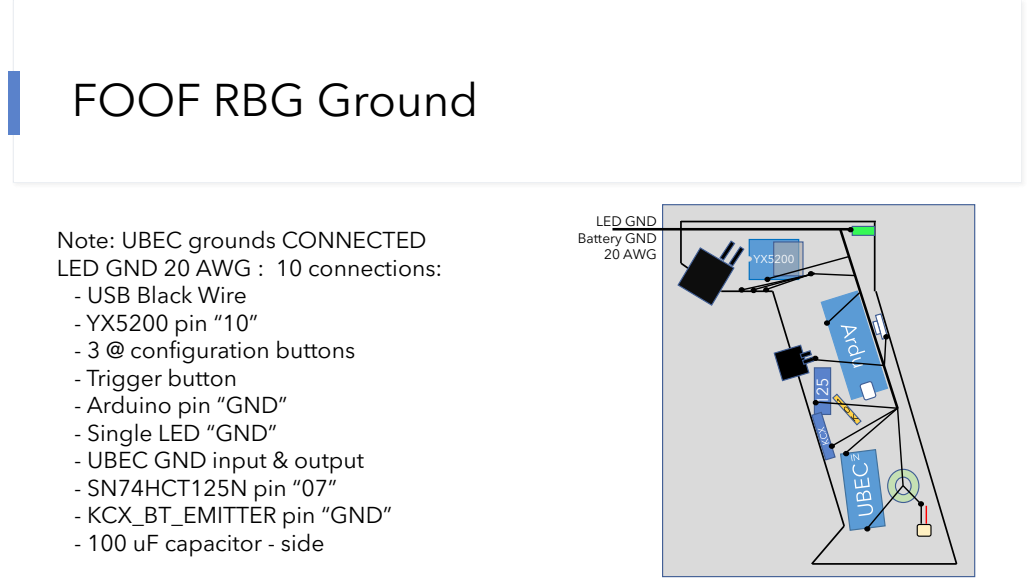
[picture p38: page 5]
LED GND Battery GND 20 AWG

Note: UBEC grounds CONNECTED
LED GND 20 AWG : 10 connections:
- USB Black Wire
- YX5200 pin “10”
- 3 @ configuration buttons
- Trigger button
- Arduino pin “GND”
- Single LED “GND”
- UBEC GND input & output
- SN74HCT125N pin “07”
- KCX_BT_EMITTER pin “GND”
- 100 uF capacitor - side

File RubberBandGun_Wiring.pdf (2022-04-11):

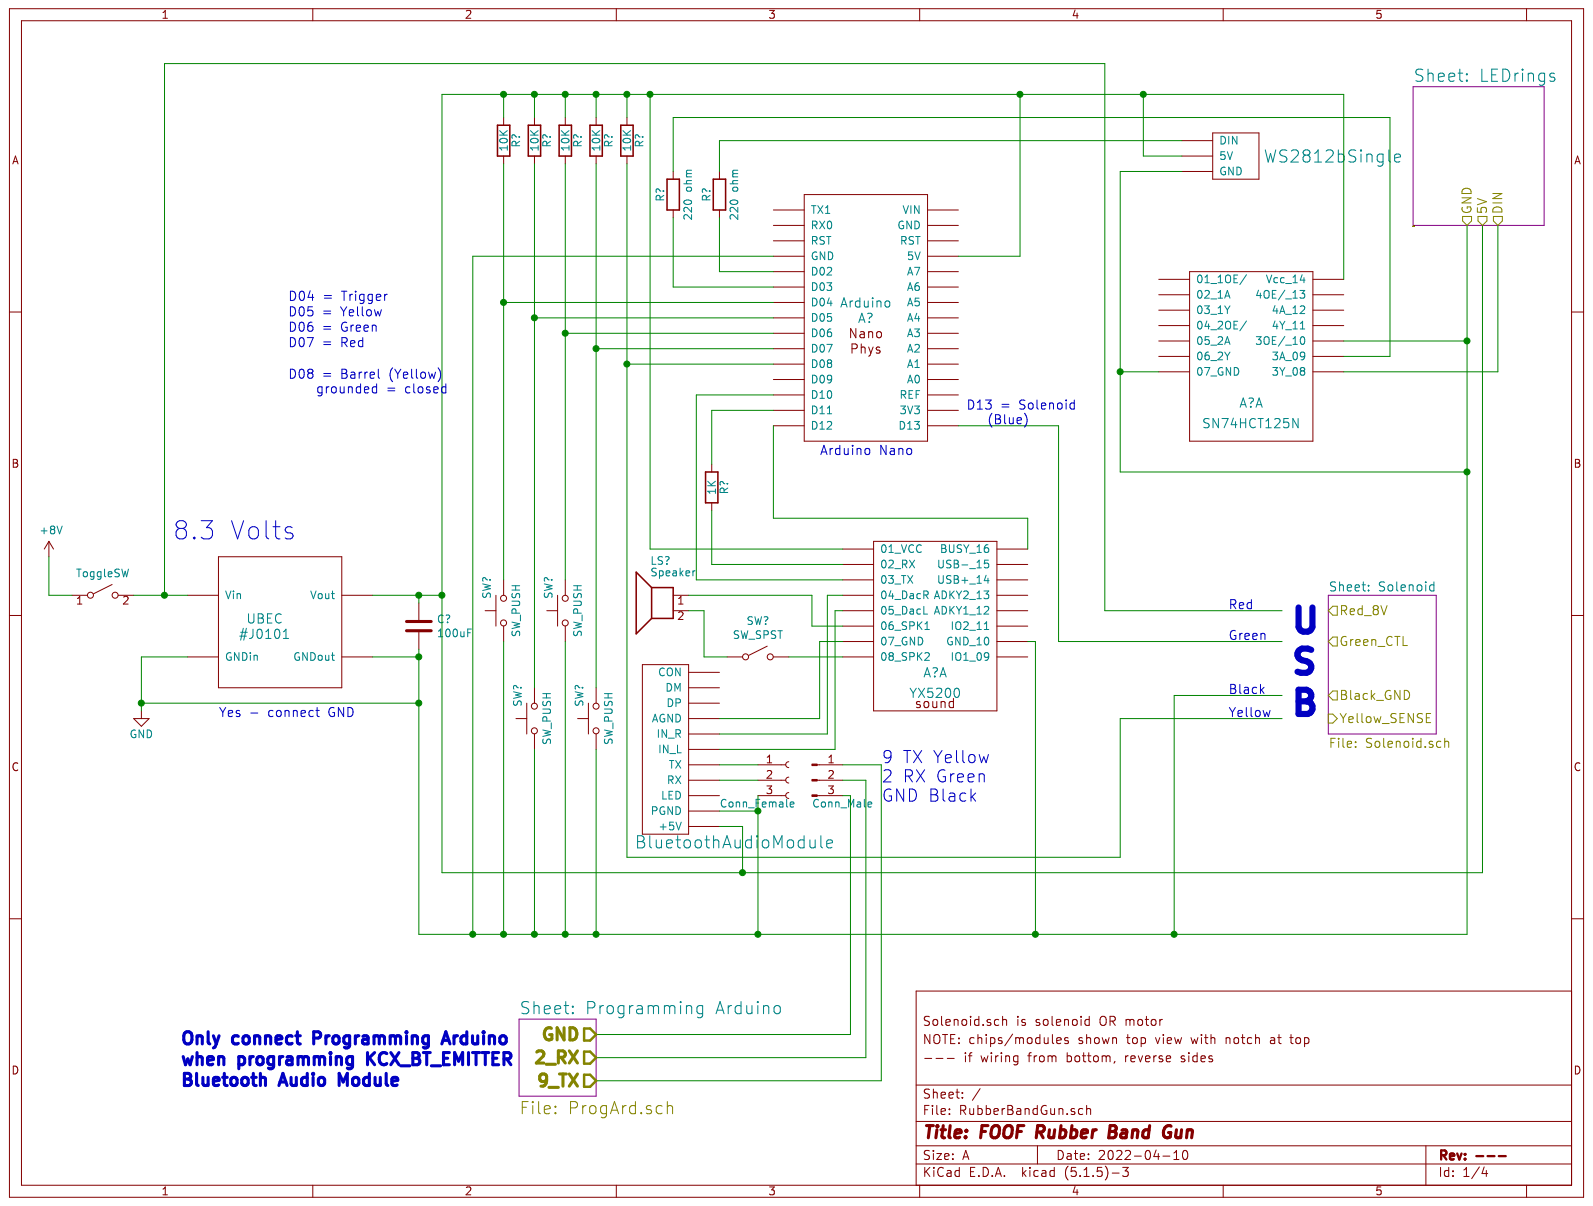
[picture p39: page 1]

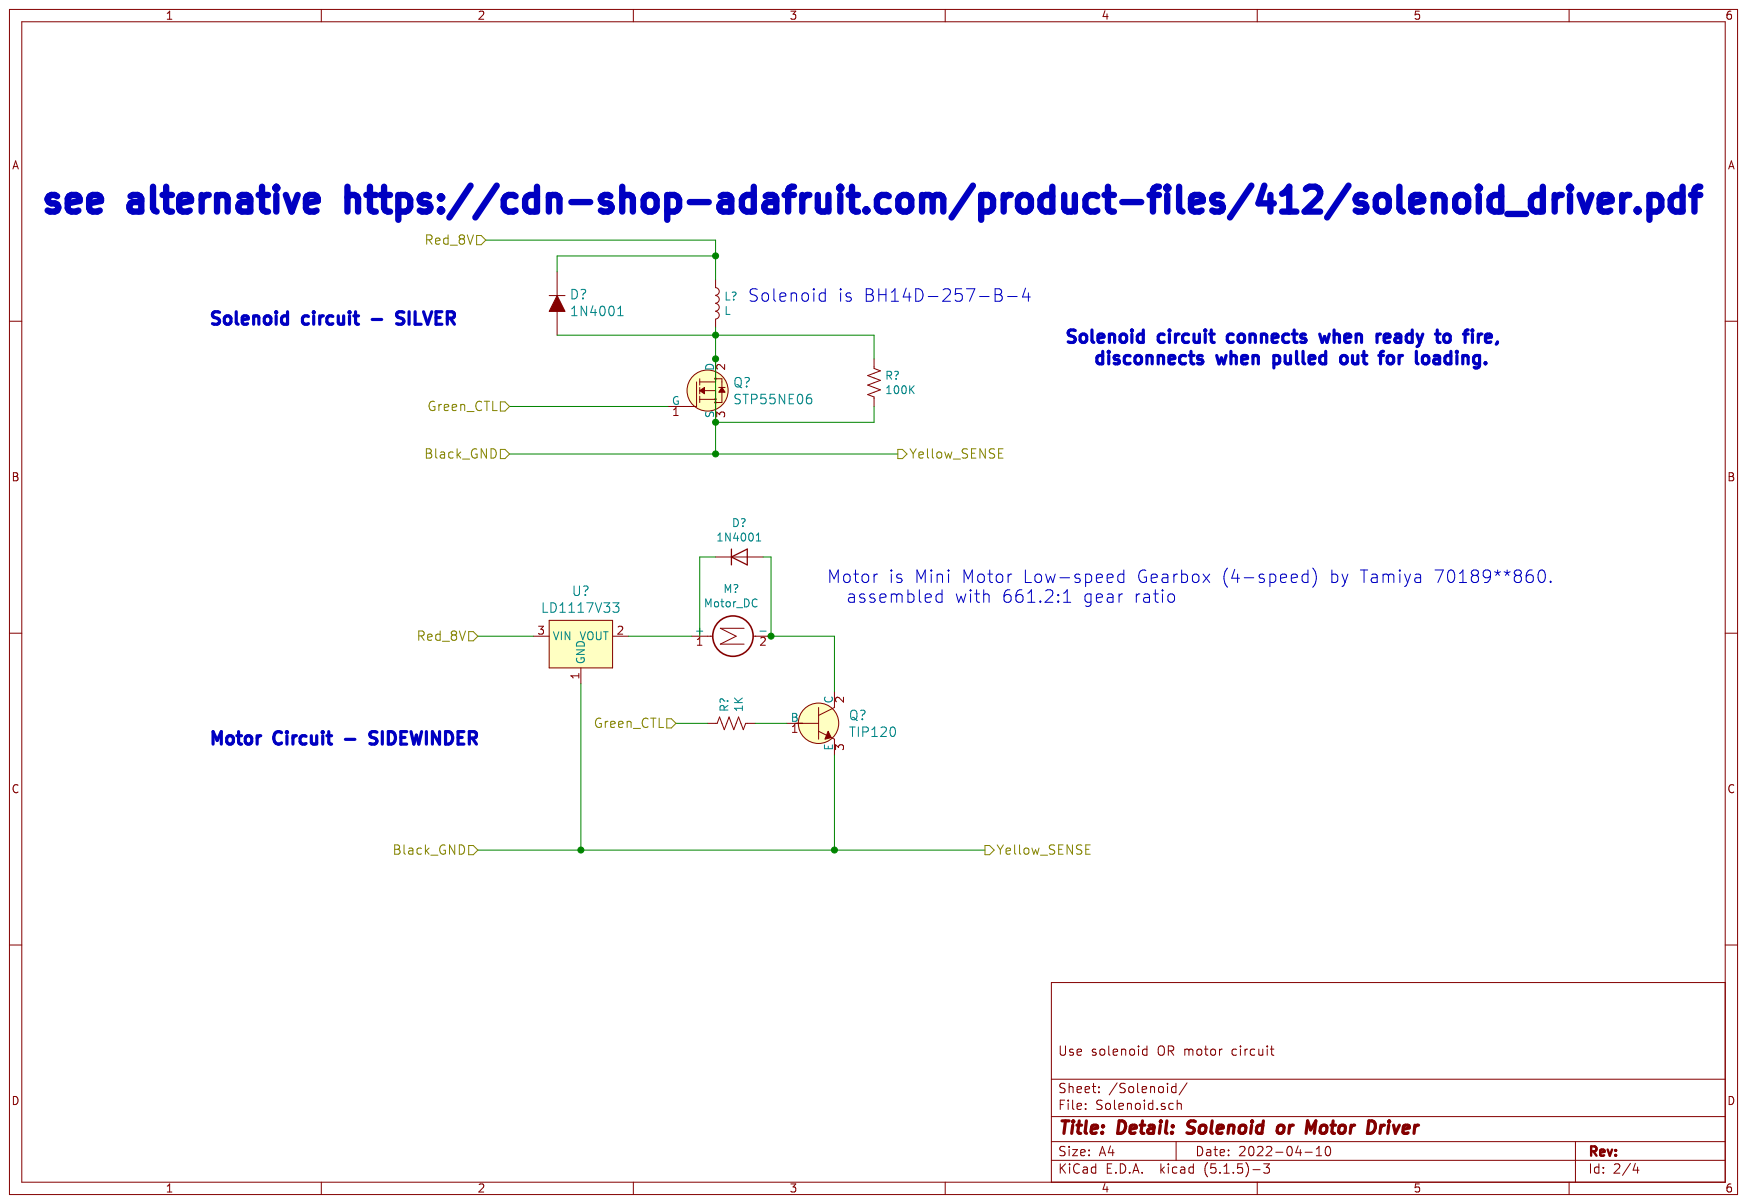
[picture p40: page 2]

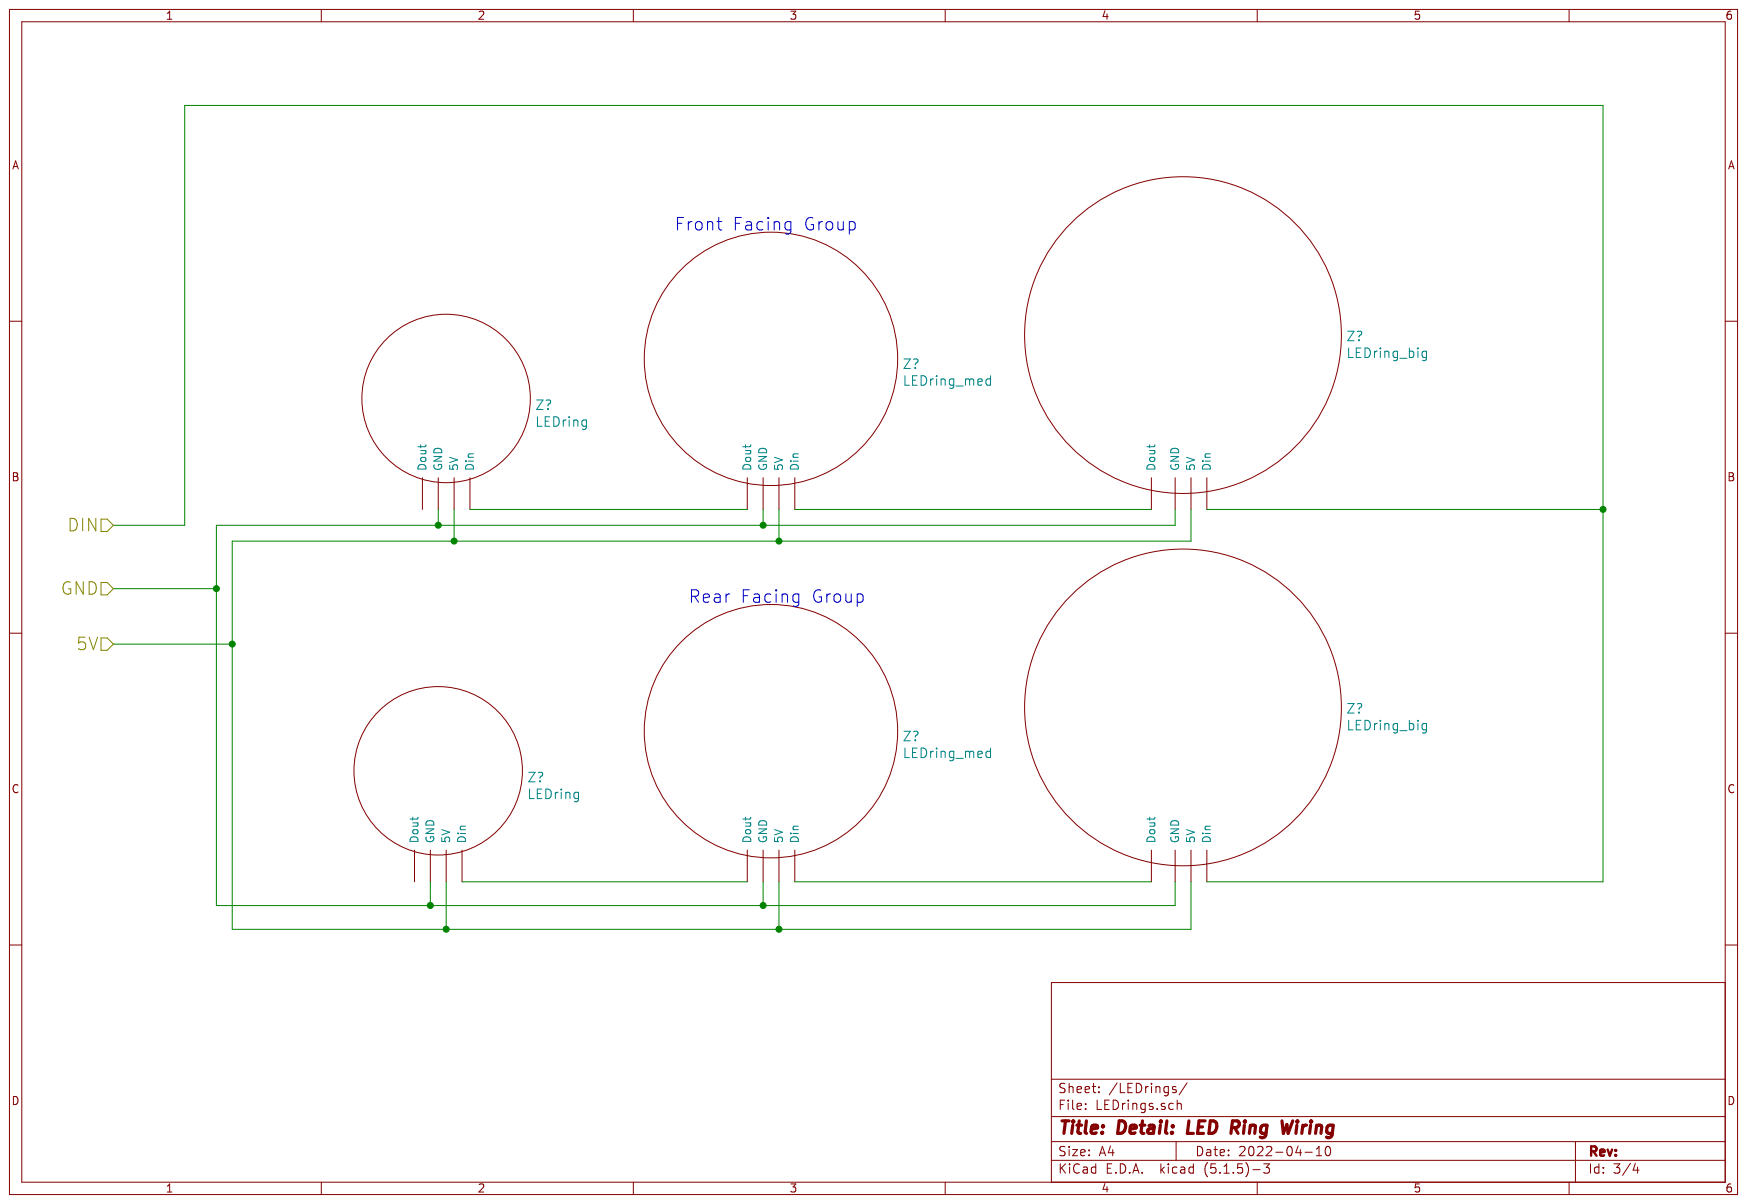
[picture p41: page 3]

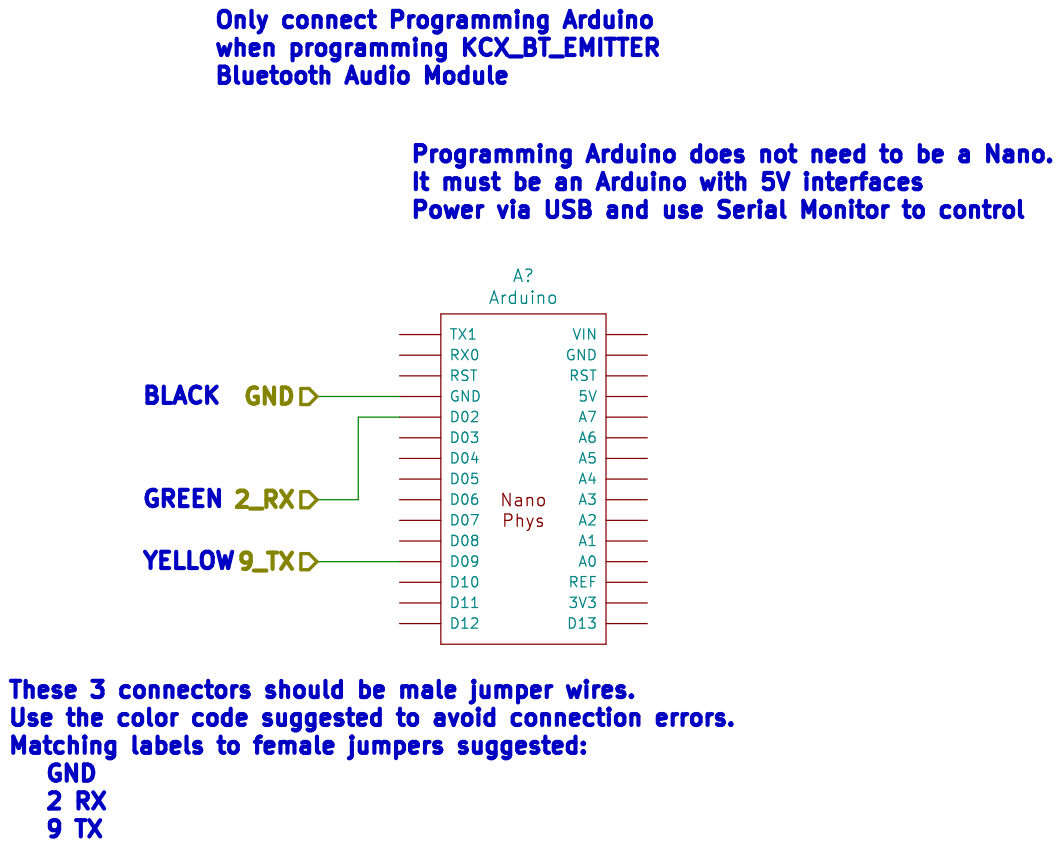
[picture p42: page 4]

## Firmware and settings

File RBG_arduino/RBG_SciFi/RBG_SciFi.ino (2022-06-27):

// Author: Mark Olson 2019-11-03
//
// Rubber Band Gun - https://github.com/Mark-MDO47/RubberBandGun
// RBG - A high-tech imagining of the rubber band gun
//
// Major kudos to Daniel Garcia and Mark Kriegsman for the FANTASTIC FastLED library and examples!!!
//    A sad note that Daniel Garcia, co-author of FastLED library, was on the dive boat that caught fire and has passed. 
//    Here is some info on the FastLED Reddit https://www.reddit.com/r/FastLED/
//
// As usual, I am using a mix of my hand-coded LED patterns plus a few from Mark Kriegsman's classic DemoReel100.ino https://github.com/FastLED/FastLED/tree/master/examples/DemoReel100
//
// I am using an Arduino Nano with a USB mini-B connector
//   example: http://www.ebay.com/itm/Nano-V3-0-ATmega328P-5V-16M-CH340-Compatible-to-Arduino-Nano-V3-Without-Cable/201804111413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
//            V3.0 ATmega328P 5V 16M CH340 Compatible to Arduino Nano V3
//            32Kbyte Flash (program storage), 2Kbyte SRAM, 1Kbyte EEPROM
//            http://www.mouser.com/pdfdocs/Gravitech_Arduino_Nano3_0.pdf
//            http://www.pighixxx.com/test/pinouts/boards/nano.pdf
//
// Using the biggest three rings of two sets of LED disks, one facing forward and one facing back: https://smile.amazon.com/gp/product/B07437X7SL/ref=ppx_yo_dt_b_asin_title_o03_s00?ie=UTF8&psc=1
//
// Also using a YX5200 sound player
//   The YX5200 uses FAT32-formatted TF (or SD ?) card up to 32 GByte
//   These look like a helpful sites for the YX5200:
//   https://wiki.dfrobot.com/DFPlayer_Mini_SKU_DFR0299
//   https://github.com/DFRobot/DFRobotDFPlayerMini
// The YX5200 interface code is based on the "FullFunction.ino" DFPlayer.
//   this uses the GNU Lesser General Public License.
//
// Thank you LIGO folks for making the fun sounds available to non-researchers!
// https://www.ligo.org/index.php
// https://www.ligo.org/detections/O1O2catalog.php
// https://www.gw-openscience.org/audiogwtc1/
// I particularly like GW170817-template.wav; it has the ramp-up and then the kick at the end.
//
// Here are the files I used, modified, and combined (or plan to use) for the sounds
// | Tag        | File Name                                      | URL                             | Who |
// | ---        | ---                                            | ---                             | --- |
// | N/A | GW170817-template.wav | https://www.gw-openscience.org/audiogwtc1/ | LIGO detectors |
// | N/A | SKR-03-324.wav | http://www-pw.physics.uiowa.edu/space-audio/cassini/SKR1/ | NASA Cassini mission Radio and Plasma Wave Science |
// | zero/1.0/ | 145209__lensflare8642__shotgun-sounds.mp3 | https://freesound.org/s/145209/ | lensflare8642 |
// | zero/1.0/ | 162814__timgormly__spaceship-4.aiff | https://freesound.org/s/162814/ | timgormly |
// | by-nc/3.0/ | 165483__timbre__glitch-voice-ep-mp3.mp3 | https://freesound.org/s/165483/ | timbre |
// | by/3.0/ | 169292__lazr2012__haywirefusionator.ogg | https://freesound.org/s/169292/ | lazr2012 |
// | zero/1.0/ | 170136__lazr2012__machinery-bo.flac | https://freesound.org/s/170136/ | lazr2012 |
// | by-nc/3.0/ | 179281__timbre__boingy-sweep.flac | https://freesound.org/s/179281/ | Timbre |
// | by/3.0/ | 216096__richerlandtv__u-f-o.mp3 | https://freesound.org/s/216096/ | RICHERlandTV |
// | by/3.0/ | 221875__hero-of-the-winds__spring-boing.wav | https://freesound.org/s/221875/ | hero-of-the-winds |
// | by/3.0/ | 240297__jalastram__abstract-guitar-sfx-003.wav | https://freesound.org/s/240297/ | jalastram |
// | by/3.0/ | 272068__ichbinjager__shotgun-action.wav | https://freesound.org/s/272068/ | IchBinJager |
// | by/3.0/ | 275537__wjoojoo__contact-mic-on-satellite-dish04.wav | https://freesound.org/s/275537/ | wjoojoo |
// | zero/1.0/ | 352852__josepharaoh99__game-style-laser-beam.wav | https://freesound.org/s/352852/ | josepharaoh99 |
// | zero/1.0/ | 380886__morganpurkis__doom-shotgun-2017.wav | https://freesound.org/s/380886/ | morganpurkis |
// | by/3.0/ | 383205__spiceprogram__loading-sound.wav | https://freesound.org/s/383205/ | SpiceProgram |
// | zero/1.0/ | 383760__deleted-user-7146007__laboratory-mad-scientist-science-fiction-sci-fi.wav | https://freesound.org/s/383760/ | deleted-user-7146007 |
// | zero/1.0/ | 397254__screamstudio__loading.wav | https://freesound.org/s/397254/ | ScreamStudio |
// | zero/1.0/ | 404068__swordofkings128__backyard-gate-open.wav | https://freesound.org/s/404068/ | swordofkings128 |
// | zero/1.0/ | 407052__sojan__power-charge.flac | https://freesound.org/s/193610/ | crashoverride61088 |
// | by/3.0/ | 417131__cuddlenucks__science-fiction-noise-3.wav | https://freesound.org/s/417131/ | cuddlenucks |
// | by/3.0/ | 417363__xcreenplay__boing-massive-kick.wav | https://freesound.org/s/417363/ | xcreenplay |
// | by/3.0/ | 431117__inspectorj__door-front-opening-a.wav | https://freesound.org/s/431117/ | inspectorj |
// | zero/1.0/ | 500418__dj-somar__intro-reverso-craver-microbrute.wav | https://freesound.org/s/500418/ | DJ_SoMaR |
// | by/3.0/ | 7967__cfork__boing-raw.aiff | https://freesound.org/s/7967/ | cfork |
// | by/3.0/ | 88635__uair01__bicycle-picture-in-spectrum.wav | https://freesound.org/s/88635/ | uair01 |
// | by-nc/3.0/ | 91296__timbre__bwaang-2-reverb.mp3 | https://freesound.org/s/91296/ | timbre |
// | by/3.0/ | 96964__gabisaraceni__porta-abrindo-5.wav | https://freesound.org/s/96964/ | gabisaraceni |
// | zero/1.0/ | 388276__csnmedia__la-cucaracha-car-horn.wav | https://freesound.org/s/388276/ | csnmedia |
// | zero/1.0/ | 118807__lmbubec__17-1985-ford-mustang-horn.wav | https://freesound.org/s/118807/ | lmbubec |
//
// | Tag        | Name                                               | URL |
// | ---        | ---                                                | --- |
// | zero/1.0/  | Creative Commons 0 License                         | https://creativecommons.org/publicdomain/zero/1.0/ |
// | by/3.0/    | Creative Commons Attribution License               | https://creativecommons.org/licenses/by/3.0/ |
// | by-nc/3.0/ | Creative Commons Attribution Noncommercial License | https://creativecommons.org/licenses/by-nc/3.0/ |
//
// The robotic voice sounds were generated using the eSpeak text to speech program found on eSpeak.SourceForge.net.
//
// Note: I am not making any claims that this software is well written or a good example for anyone.
//       I am just having fun with it.
//       Mark


#include "Arduino.h"
#include "SoftwareSerial.h"                  // to talk to myDFPlayer without using up debug serial port
#include <EEPROM.h>                          // to store configuration info

#define USE_PROGMEM true                     // set true to keep big const items in FLASH (PROGMEM keyword)

#include "FastLED.h"                         // to manipulate WS2812b (NeoPixel) 5050 RGB LED Rings
#include "DFRobotDFPlayerMini.h"             // to communicate with the YX5200 audio player

#include "RBG_SciFi_StatesAndInputs.h"       // state tables and input definitions
#include "RBG_SciFi_LEDs.h"                  // LED structural and pattern definitions

#define SERIALDEBUG 1                        // serial debugging
#define REAL_BUTTONS 1                       // use actual buttons

#define DEBUG_SHOW_MSEC 1                    // use globalLoopCount for millis() display not loopcount
#define DONOTEXPLAINBITS 1                   // don't explain the bits - existing routine uses too much RAM

#define DEBUGALL_GLOBAL 0                    // sets many of the following
#define DEBUG_STATE_MACHINE (0 | DEBUGALL_GLOBAL) // 1 to show state machine internals for transitions
#define DEBUG_INPUTS (1 | DEBUGALL_GLOBAL)        // 1 to show all inputs MDO_DEBUG_TURNOFFLATER
#define DEBUG_CONFIG (0 | DEBUGALL_GLOBAL)        // 1 to show all CONFIGURATION special activity
#define DEBUG_TRIGSTATE (1 | DEBUGALL_GLOBAL)     // 1 to show all new trigger state activity

static uint32_t globalLoopCount = 0;  // based on DEBUG_SHOW_MSEC: this is either the milliseconds since startup or a count of times through loop()

SoftwareSerial mySoftwareSerial(DPIN_SWSRL_RX, DPIN_SWSRL_TX); // to talk to YX5200 audio player
DFRobotDFPlayerMini myDFPlayer;                                // to talk to YX5200 audio player
void DFsetup();                                                // how to initialize myDFPlayer

// sure glad we are done with debugging the YX5200 and its code!!!
//
#define DFPRINTDETAIL (1&SERIALDEBUG)     // if need detailed status from myDFPlayer
// #define DFPRINTDETAIL 0                      // will not print detailed status from myDFPlayer
#if DFPRINTDETAIL // routine to do detailed debugging
  void DFprintDetail(uint8_t type, int value); // definition of call
#else  // no DFPRINTDETAIL
  #define DFprintDetail(type, value) // nothing at all
#endif // #if DFPRINTDETAIL


static uint8_t gHue = 0; // rotating "base color" used by Demo Reel 100
CRGBPalette16 gPal; // palette for Fire2012WithPalette()
static uint16_t gSeed = ((uint16_t) 42); // my favorite is 47 but the whole world loves 42 and HHG2TG
// we are not using the fire pattern
#if FASTLED_FIRE_PATTERN // only used for Fire pattern
CRGB dark_color_palette[1]  = { CRGB::DarkGreen, CRGB::Red,    CRGB::Blue, CRGB::DarkOrange };
CRGB light_color_palette[1] = { CRGB::LimeGreen, CRGB::Yellow, CRGB::Aqua, CRGB::Gold };
#endif // FASTLED_FIRE_PATTERN

static uint16_t nowVinputRBG; // latest button inputs, to compare with previous in myState

static RBGStateTable_t loopRow; // for use in setup() and loop() - since USE_PROGMEM, must copy to RAM 

/////////////////////////////////////////////////////////////////////////////////////////////////////////
// setup()
//   initializes hardware serial port for general debug
//   initializes SoftwareSerial for DFPlayer audio player YX5200 control
//   initializes push button pins
//   initializes FastLED library
void setup() {
  // put your setup code here, to run once:

  // take care of the solenoid output pin ASAP
  pinMode(DPIN_SOLENOID,   OUTPUT);        // fires the rubber band
  // make sure solenoid or motor is not drawing power
  RBG_specialProcStopShoot(0); // serial port not initialized yet don't do debug printing

#if USE_PROGMEM   
  memcpy_P(&loopRow, &myStateTable[myState.tableRow], sizeof(myStateTable[0]));
#else // not USE_PROGMEM
  memcpy(&loopRow, &myStateTable[myState.tableRow], sizeof(myStateTable[0]));
#endif // use, not USE_PROGMEM

  Serial.begin(115200);         // this is for general debug

  while (!Serial) {
    ; // wait for serial port to connect. Needed for native USB port only
  }
  Serial.println();
  Serial.println(F("FOOF SciFi RBG init...")); 

  mySoftwareSerial.begin(9600); // this is control to DFPlayer audio player

  // initialize the input pins. Not sure if my Nano actually has a pullup...
  //    fortunately the RBG controller board has a 10K pullup resistor
  pinMode(DPIN_BTN_TRIGGER, INPUT_PULLUP); // trigger
  pinMode(DPIN_BTN_YELLOW,  INPUT_PULLUP); // configuration button
  pinMode(DPIN_BTN_GREEN,   INPUT_PULLUP); // configuration button
  pinMode(DPIN_BTN_RED,     INPUT_PULLUP); // configuration button
  pinMode(DPIN_AUDIO_BUSY,  INPUT_PULLUP); // tells when audio stops
  pinMode(DPIN_LOCK_LOAD,   INPUT_PULLUP); // tells if barrel is locked and loaded
  // and the other output pin
  pinMode(DPIN_UNUSED,      INPUT_PULLUP); // matches with BlueToothTesting.ino

  // initialize the DFPlayer audio player
  DFsetup();

  // initialize the FastLED library for our setup
  // according to Amazon comments: Library configuration used was WS2812B GRB (not RGB). Library call: FastLED.addLeds<WS2812B, DATA_PIN, GRB>(leds, NUM_LEDS);. Everything worked as expected.
  //    this was for the graduation cap: FastLED.addLeds<NEOPIXEL,DPIN_FASTLED>(led_display, NUM_LEDS_PER_DISK);
  FastLED.addLeds<WS2812B,DPIN_FASTLED,GRB>(led_display, NUM_LEDS_PER_DISK);
  FastLED.addLeds<WS2812B,DPIN_FASTLED_SNGL,GRB>(&led_sngl, 1);
  FastLED.setBrightness(BRIGHTMAX); // we will do our own power management
  // initialize led_display
  RBG_diskInitBrightSpots(windup1BrightSpots, &led_BLACK, 3, 196); // FIXME need initialize for this pattern

  // initialize FASTLED_SNGL to do the single LED inside the handle
  fill_rainbow( led_sngl_array, FASTLED_SNGLPTRNLEN, gHue, 21); // this just fills up the colors to send later
  led_sngl = led_sngl_array[0]; // load first color
  
  // if needed, initialize EEPROM variables
  eeprom_check_init(EEPROM_PROCESS_ALL_CONFIG);
  copy_eeprom_to_ram_running_config(EEPROM_CONFIG_RUNNING);
  // eeprom_factory_init(EEPROM_PROCESS_ALL_CONFIG);

  printAllMyState();
  printAllMyInputs();
  Serial.println(F("FOOF SciFi RBG init COMPLETE\n"));

} // end setup()

/////////////////////////////////////////////////////////////////////////////////////////////////////////
//  loop()
//     Get the inputs - buttons, barrel, sound ended
//     Use our state table and state and inputs to calculate next state
//     Determine if we need to change LED pattern and/or sound
//     If needed, release the rubber band and set timer to stop the solenoid current later
//
void loop() {

#if USE_PROGMEM   
  memcpy_P(&loopRow, &myStateTable[myState.tableRow], sizeof(myStateTable[0]));
#else // not USE_PROGMEM
  memcpy(&loopRow, &myStateTable[myState.tableRow], sizeof(myStateTable[0]));
#endif // use, not USE_PROGMEM

  // put your main code here, to run repeatedly:

  static uint16_t preVinputRBG = 65535;

  myState.timerNow = millis();
  #if DEBUG_SHOW_MSEC
  globalLoopCount = myState.timerNow;
  #endif // DEBUG_SHOW_MSEC


  // handle (most of) solenoid OFF or motor OFF processing
  // Four factors: SOLENOID_IF_NONZERO, DLYSOLENOID_MIN and _MAX, releasing the trigger
  //   SOLENOID/CLOTHESPIN approach - ignore the trigger, just use the edge signal to start
  //                         hold the solenoid for at least DLYSOLENOID_MIN milliseconds
  //                         after that, when shooting sound finishes, then release the solenoid
  //                         release the solenoid after DLYSOLENOID_MAX milliseconds no matter what
  //   MOTOR/SIDEWINDER approach - we also take into account how long the trigger is held in
  //                         run the motor for at least DLYSOLENOID_MIN milliseconds
  //                         after that, when the trigger is released, stop the motor
  //                         stop the motor after DLYSOLENOID_MAX milliseconds no matter what
  // NOTE: this part does not depend on getButtonInput() and should happen immediately if conditions are met
  if ((myState.timerMaxForceSolenoidLow > 0) && (myState.timerNow > myState.timerMinForceSolenoidLow)) { // shooting and passed minimum
    if (myState.timerNow > myState.timerMaxForceSolenoidLow) {
      if (DEBUG_TRIGSTATE) { Serial.print(F("DEBUG TRIGSTATE 01 RBG_specialProcStopShoot() - nowVinputRBG 0x"));Serial.println(nowVinputRBG, HEX);  printAllMyState(); Serial.print(F(" loopCount ")); Serial.println(globalLoopCount); }
      RBG_specialProcStopShoot(SERIALDEBUG); // always turn off after maximum delay
    }
  }

  // see if time to run the state machine and process inputs
  if ((myState.timerNow-myState.timerPrevState) >= 40) { // || (myState.VinputRBG != nowVinputRBG)) { THIS MAKES RELEASING TRIGGER TOO FAST AFFECT SOUND START
    nowVinputRBG = getButtonInput();
    if (myState.timerMaxForceSolenoidLow > 0) { // shooting
      if ((SOLENOID_IF_NONZERO || (0 == (mVINP_TRIG_STATE & nowVinputRBG))) && (myState.timerNow > myState.timerMinForceSolenoidLow)) {
        if (DEBUG_TRIGSTATE) { Serial.print(F("DEBUG TRIGSTATE 02 RBG_specialProcStopShoot() - nowVinputRBG 0x")); Serial.println(nowVinputRBG, HEX);  printAllMyState(); Serial.print(F(" loopCount ")); Serial.println(globalLoopCount); }
        RBG_specialProcStopShoot(SERIALDEBUG); // (SOLENOID || trigger released), sound finished, beyond minimum time
      }
    }
    if (preVinputRBG != nowVinputRBG) {
      Serial.print(F("DEBUG loop() - nowVinputRBG 0x")); Serial.print(nowVinputRBG, HEX); Serial.print(F(" loopCount ")); Serial.println(globalLoopCount);
    }
    preVinputRBG = nowVinputRBG;
    nowVinputRBG = RBG_processStateTable(nowVinputRBG);
    myState.timerPrevState = myState.timerNow;
    myState.VinputRBG = nowVinputRBG;
  } // end wait for next State activity

  // see if time to run the LED patterns
  dwell_led_sngl -= 1; // process the single LED in the handle
  if (dwell_led_sngl < 0) {
    dwell_led_sngl = FASTLED_SNGLDWELL;
    led_sngl = led_sngl_array[which_led_sngl];
    which_led_sngl += 1;
    if (which_led_sngl >= FASTLED_SNGLPTRNLEN) { which_led_sngl = 0; }
  }
  if ((myState.timerNow-myState.timerPrevLEDstep) >= myState.ptrnDelayLEDstep) {
    gHue += 3; // rotating "base color" used by Demo Reel 100 patterns
    checkDataGuard();
    doPattern(loopRow.efctLED, loopRow.SPECIAL, 0); // start
    checkDataGuard();
    FastLED.show();
    myState.timerPrevLEDstep = myState.timerNow;
    globalLoopCount += 1;
  } // end wait for next LED activity

}  // end loop()

// ******************************** LED UTILITIES ****************************************

/////////////////////////////////////////////////////////////////////////////////////////////////////////
// doPattern(tmpEfctLED, tmpSpecial, tmpInit) - start or step the pattern
//
// If tmpInit is nonzero, do initialization of pattern
// If tmpSpecial says mSPCL_EFCT_CONFIGURE and efctSound == mNONE and cfg_curnum != mNONE then we use the configuration variables
// If tmpEfctLED is an EEPROM configurable pattern (divisible by 10) then configure it
//
#define DEBUG_DPtrn 0
//
void doPattern(uint16_t tmpEfctLED, uint16_t tmpSpecial, uint8_t tmpInit) {
//  static uint16_t prevEfctLED = mNONE;
  static uint16_t numSteps = 0;
  uint16_t nowEfctLED = tmpEfctLED & 0x00FF; // just the effect number

  #if DEBUG_DPtrn
  Serial.print(F(" DEBUG doPattern BEFORE tmpEfctLED ")); Serial.print(tmpEfctLED); Serial.print(F(" tmpInit ")); Serial.print(tmpInit); Serial.print(F(" final nowEfctLED ")); Serial.print(nowEfctLED); Serial.println(F(" that is all"));
  #endif // DEBUG_DPtrn

  if ((mNONE == nowEfctLED) && (0 != (mSPCL_EFCT_CONFIGURE & tmpSpecial)) && (mNONE != myState.cfg_curnum)) {
    // handle configuration choice effects
    nowEfctLED = myState.cfg_curnum + myState.cfg_type2save;
  } else if ((mNONE != nowEfctLED) && (EFCT_IS_EEP(nowEfctLED)) && (nowEfctLED <= mEFCT_LAST_EEP_CONFIG)) {
    // configurable LED patterns are zero mod 10; we get config from EEPROM
    // nowEfctLED += EEPROM.read(EEPOFFSET(nowEfctLED)+EEPROM_START_LED_CONFIGS); old way; now using EEPROM_RAMcopy
    nowEfctLED += EEPROM_RAMcopy[EEPOFFSET(nowEfctLED)+EEPROM_START_LED_CONFIGS];
  } // end if configurable LED pattern

  // now convert "configuration" effect number to pattern effect number
  #if DEBUG_DPtrn
  Serial.print(F(" DEBUG doPattern BEFORE lookupLEDpattern tmpEfctLED ")); Serial.print(tmpEfctLED); Serial.print(F(" tmpInit ")); Serial.print(tmpInit); Serial.print(F(" final nowEfctLED ")); Serial.print(nowEfctLED);
  Serial.print(F(" lookup(-1) ")); Serial.print(lookupLEDpattern(nowEfctLED-1)); Serial.print(F(" lookupLEDpattern lookup(+0) ")); Serial.print(lookupLEDpattern(nowEfctLED)); Serial.print(F(" lookupLEDpattern lookup(+1) ")); Serial.println(lookupLEDpattern(nowEfctLED+1)); 
  #endif // DEBUG_DPtrn
  nowEfctLED = lookupLEDpattern(nowEfctLED);
  tmpEfctLED = (0xFF00 & tmpEfctLED) | nowEfctLED;

  #if DEBUG_DPtrn
  Serial.print(F(" DEBUG doPattern AFTER  lookupLEDpattern tmpEfctLED ")); Serial.print(tmpEfctLED); Serial.print(F(" tmpInit ")); Serial.print(tmpInit); Serial.print(F(" final nowEfctLED ")); Serial.println(nowEfctLED);
  #endif // DEBUG_DPtrn

  switch (nowEfctLED) {

    case mEFCT_PTRNLED_OFF: // 254 = OFF
    default:
      if (0 != tmpInit) { // initialize
        for (uint8_t idx = 0; idx < NUM_RINGS_PER_DISK; idx++) {
          led_display[idx] = CRGB::Black;
        }
      } // there is no "step"; just leave the LEDs off
      break;

    case 1:
      juggle();
      break;

    case 2:
      rainbowWithGlitter();
      break;

    case 3:
      RBG_bpm_rings();
      break;

    case 4: // RBG_diskDownTheDrainOrRotate(-1) disk, clockwise, rotate through
      if (0 != tmpInit) { // initialize
        RBG_ringRotateAndFade(mNONE, 0, windup1BrightSpots); // FIXME - initialization from other effect
        RBG_diskDownTheDrainOrRotate(0);
      } else { // step
        RBG_diskDownTheDrainOrRotate(-1);
      }
      break;

    case 5: // RBG_diskDownTheDrainOrRotate(2) disk, counterclockwise, drain, repeat
      if ((0 != tmpInit) || (numSteps > (10+NUM_LEDS_PER_DISK))) { // initialize
        RBG_ringRotateAndFade(mNONE, 0, windup1BrightSpots); // FIXME - initialization from other effect
        numSteps = 0;
      } else { // step
        RBG_diskDownTheDrainOrRotate(2);
        numSteps += 1;
      }
      break;

    case 6: // RBG_juggle_numdot_ring(-4) rings, 4 dots
      RBG_juggle_numdot_ring(-4);
      break;

    case 7: // RBG_juggle_numdot_ring(5); RBG_confetti_fadeby(128); disk, 5 dots, sparkle confetti
      RBG_juggle_numdot_ring(5);
      RBG_confetti_fadeby(128);
      break;

    case 8:
      RBG_RailGunEffect(tmpInit, &led_BLUE);
      break;

    case 9:
      RBG_RailGunEffect(tmpInit, &led_RED);
      break;

    case 10:
      RBG_RailGunEffect(tmpInit, &led_GREEN);
      break;

    case 11:
      RBG_confetti_fadeby(128);
      break;

    case 12:
      bpm();
      break;

    case 13:
      confetti();
      break;
  } // end switch
} // end doPattern()
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

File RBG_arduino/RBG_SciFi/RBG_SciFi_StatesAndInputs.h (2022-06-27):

// Mark Olson 2020-08
//
// Major kudos to Daniel Garcia and Mark Kriegsman for the FANTASTIC FastLED library and examples!!!
//    A sad note that Daniel Garcia, co-author of FastLED library, was on the dive boat that caught fire and has passed. 
//    Here is some info on the FastLED Reddit https://www.reddit.com/r/FastLED/
//
// I am using an Arduino Nano with a USB mini-B connector
//   example: http://www.ebay.com/itm/Nano-V3-0-ATmega328P-5V-16M-CH340-Compatible-to-Arduino-Nano-V3-Without-Cable/201804111413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
//            V3.0 ATmega328P 5V 16M CH340 Compatible to Arduino Nano V3
//            32Kbyte Flash (program storage), 2Kbyte SRAM, 1Kbyte EEPROM
//            http://www.mouser.com/pdfdocs/Gravitech_Arduino_Nano3_0.pdf
//            http://www.pighixxx.com/test/pinouts/boards/nano.pdf
//
// Using the biggest three of two sets of LED rings: https://smile.amazon.com/gp/product/B07437X7SL/ref=ppx_yo_dt_b_asin_title_o03_s00?ie=UTF8&psc=1
//
// Here is a (somewhat) spec on the 2812b LEDs: https://cdn-shop.adafruit.com/datasheets/WS2812B.pdf
// Here is a Worldsemi WS2812B document for download: http://www.world-semi.com/solution/list-4-1.html#108
//
// Kudos to Daniel Garcia and Mark Kriegsman for the FANTASTIC Arduino FastLED library and examples!!!
//    https://github.com/FastLED/FastLED
//    https://github.com/FastLED/FastLED/blob/master/examples/Fire2012WithPalette/Fire2012WithPalette.ino
//
// This file has definitions for state tables and input processing (mostly buttons)
//

#define NUMOF(x) (sizeof((x)) / sizeof((*x)))

template <typename T> int sgn(T val) {
    return (T(0) < val) - (val < T(0));
} // returns -1, 0, 1 for (T < 0), (T == 0), (T > 0) respectively. returns warning if used on uintx_t

#define DPIN_FASTLED_SNGL 2  // serial out - talk to single LED in handle
#define NO_FASTLED_SNGL   0  // 1=do not actually write to pin 2, 0=normal

#define DPIN_FASTLED      3  // serial out - talk to LED rings
#define DPIN_BTN_TRIGGER  4  // digital input - the trigger (we only count once per trigger press)
#define DPIN_BTN_YELLOW   5  // digital input - yellow configuration button
#define DPIN_BTN_GREEN    6  // digital input - green configuration button
#define DPIN_BTN_RED      7  // digital input - blue configuration button
#define DPIN_LOCK_LOAD    8  // digital input - grounded when in lock and load position
#define DPIN_UNUSED       9  // digital input - pair the BlueTooth Audio Transmitter
#define DPIN_SWSRL_RX    10  // serial in  - talk to DFPlayer audio player (YX5200)
#define DPIN_SWSRL_TX    11  // serial out - talk to DFPlayer audio player (YX5200)
#define DPIN_AUDIO_BUSY  12  // digital input - signals when audio finishes
#define DPIN_SOLENOID    13  // often has internal LED and resistor soldered to board, can make INPUT not work


/////////////////// start -> INPUTS 1 FROM makeStateTable.py <- //////////////////////////////////

// define the symbols - general use symbols:
#define mUNDEFINED 254
#define mNONE 255
#define mZERO 0

// define the symbols - .SPECIAL:
#define mSPCL_EFCT_NONE       0x8000 // set this bit for no jump and no continuous sound
#define mSPCL_EFCT_ONETIME    0x4000 // set this bit for onetime sound play then jump while waiting for other input or sound end
#define mSPCL_EFCT_CONTINUOUS 0x2000 // set this bit for continuous sound play while waiting for other input
#define mSPCL_EFCT_CONFIGURE  0x1000 // set this bit to use configuration variables instead of EEPROM and do continuous
#define mSPCL_HANDLER         0x0080 // mask for functions is ((uint16_t) (mSPCL_HANDLER-1))
#define mSPCL_HANDLER_SHOOT        2 // solenoid ON
#define mSPCL_HANDLER_SOLENOID     3 // solenoid OFF
#define mSPCL_HANDLER_CFGSTART     4 // configuration - store value at address
#define mSPCL_HANDLER_CFGNEXT      5 // configuration - go to next value at address
#define mSPCL_HANDLER_CFG2STORAGE  6 // configuration - install current config num in EEPROM or myState
#define mSPCL_HANDLER_CFG2STORAGESKIP 7 // configuration - store current config num in EEPROM or myState, skip number based on choice
#define mSPCL_HANDLER_CFG2CPYRST   8 // configuration - use current config num to manage EEPROM with copy or reset, then clear out configuration states
#define mSPCL_HANDLER_FACT2RUN     9 // configuration - factory setting to running configuration
#define mSPCL_HANDLER_FACT2ALL    10 // configuration - factory setting to all saved configuration
#define mSPCL_HANDLER_RUN2ONE     11 // configuration - running configuration to saved config one
#define mSPCL_HANDLER_RUN2TWO     12 // configuration - running configuration to saved config 
#define mSPCL_HANDLER_RUN2THREE   13 // configuration - running configuration to saved config 
#define mSPCL_HANDLER_ONE2RUN     14 // configuration - saved configuration one to running config
#define mSPCL_HANDLER_TWO2RUN     15 // configuration - saved configuration two to running config
#define mSPCL_HANDLER_THREE2RUN   16 // configuration - saved configuration three to running config
#define mSPCL_HANDLER_CFG2ADVNCD  17 // configuration - advanced menu: the selection/skip function
#define mSPCL_HANDLER_STATICMODE  18 // configuration - advanced menu: static-mode
#define mSPCL_HANDLER_ADVFEATURES 19 // configuration - advanced menu: ADVANCED features

// these are used with mSPCL_HANDLER_START and _NEXT
#define mADDR_CFG_CATEGORY         1 // for looping through SOUND or LED PATTERN
#define mADDR_CFG_TYPE             2 // for looping through number groups: shooting, open, close, etc.
#define mADDR_CFG_EFFECT           3 // for looping through the effects for that CATEGORY and TYPE
#define mADDR_CFG_CPY_RST          4 // configuration copies and factory resets
#define mADDR_CFG_ADVANCED         5 // advanced configuration
#define mEFCT_TYPE_CFG_STOREADDR_MAX mADDR_CFG_ADVANCED // .storeAddr - maximum value

// define the symbols - .blkFlags:
#define mBLOCKSTART 0x80
#define mBLOCKEND   0x40
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

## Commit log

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2019-08-16 Hmmm - diameter = 2*radius
    [RubberBandGun.scad]
2019-08-18 add crude clothespin trigger
    [RubberBandGun.scad]
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2019-09-14 updates to schematic, remove some GradCap stuff
    [GradCapWiring.sch, RubberBandGun.sch, RubberBandWiring.sch]
2019-09-14 first cut wiring diagram
    [RubberBandGun.sch]
2019-09-14 wire 5V to sound chip
    [RubberBandGun.sch]
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2019-09-30 switch from WT488D (obsolete) to YX5200
    [RubberBandGun.sch]
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2019-11-05 elaboration of state machine
    [ConfigurationMenu.xlsx]
2019-11-09 start adding in state table
    [ConfigurationMenu.xlsx, StateTable.xlsx]
2019-11-10 latest state table spreadsheet
    [StateTable.xlsx]
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2019-11-18 starting to produce C-language struct
    [StateTable.xlsx]
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2019-11-23 no compile errors but not functional
    [RBG_SciFi.ino]
2019-11-24 starting to fill in pieces
    [StateTable.xlsx, StateTable_minimal.xlsx]
2019-12-02 start adding in the LED operations
    [StateTable_minimal.xlsx]
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2019-12-05 fix references to be within myState and start adding some button processing from GradCap; will change it later
    [RBG_SciFi.ino]
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2019-12-07 reverse polarity of input flags, add RBG_waitForInput
    [RBG_SciFi.ino, RBG_SciFi_StatesAndInputs.h]
2019-12-08 rename some things, use EEPROM config
    [StateTable.xlsx, StateTable_minimal.xlsx]
2019-12-08 re-organize the mSPCL_ processing
    [StateTable.xlsx, StateTable_minimal.xlsx]
2019-12-13 finally made decision on where to put EFCT_special calls
    [StateTable.xlsx, StateTable_minimal.xlsx]
2019-12-13 start disambiguating the mXXX_xxx #defines
    [StateTable.xlsx, StateTable_minimal.xlsx]
2019-12-13 make use of state table to simplify special handlers
    [StateTable_minimal.xlsx]
2019-12-14 skeletons for RBG_specialProcSolenoid() and RBG_specialProcShoot()
    [StateTable_minimal.xlsx]
2019-12-14 continue moving flags to most logical position and refactoring code
    [StateTable.xlsx, StateTable_minimal.xlsx]
2019-12-19 RBG_debuggable now makes complete *.cpp file for MS VS
    [StateTable.xlsx]
2019-12-20 a fair bit of reshuffling
    [StateTable.xlsx, StateTable_minimal.xlsx]
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2019-12-20 fix some flaws in special processing
    [StateTable.xlsx, StateTable_minimal.xlsx]
2019-12-21 debugging finds: YX5200 does not want to play same sound number twice, still need to do fix
    [RBG_SciFi.ino, RBG_SciFi_StatesAndInputs.h]
2019-12-21 attempt to solve YX5200 issue not play same file twice
    [RBG_SciFi.ino, RBG_SciFi_StatesAndInputs.h]
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2019-12-24 somewhat fixes continuous: short delay. Still issue going back to state 1
    [StateTable_minimal.xlsx]
2019-12-24 still debugging special processing
    [StateTable_minimal.xlsx]
2019-12-25 state table seems to work; still issues with reliably starting sound
    [StateTable_minimal.xlsx]
2019-12-25 still more debugging on YX5200...
    [StateTable_minimal.xlsx]
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2019-12-25 going back to primitive play() command makes it work much better; still curiosities
    [StateTable_minimal.xlsx]
2019-12-26 pretty close to working
    [StateTable_minimal.xlsx]
2019-12-27 adjust state table for lock/open
    [StateTable.xlsx, StateTable_minimal.xlsx]
2019-12-27 numerically sort symbols, implemnet state table for open/lock
    [StateTable.xlsx, StateTable_minimal.xlsx]
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2019-12-28 major re-write, depend on rows not state inproc
    [StateTable_minimal.xlsx]
2019-12-28 fix a couple of typos
    [StateTable_minimal.xlsx]
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2019-12-29 some more sounds and a sound attribution correction
    [StateTable_minimal.xlsx]
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2020-01-01 fix bug in clockwise down the drain
    [StateTable_minimal.xlsx]
2020-01-01 still an issue with clockwise doing down the drain
    [StateTable_minimal.xlsx]
2020-01-01 fixed several issues, still doing down the drain
    [StateTable_minimal.xlsx]
2020-01-01 removed most debugging, updated rules tab in spreadsheet
    [StateTable_minimal.xlsx]
2020-01-02 rework the LED routines; after a while reaches one that doesn't move
    [StateTable_minimal.xlsx]
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2020-01-03 found my induced bug in the juggle() pattern
    [RBG_SciFi.ino, RBG_SciFi_LEDs.h, RBG_SciFi_StatesAndInputs.h]
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2020-01-05 get rid of mEFCT_CONFIGURE as an EEPROM-configurable item; use mEFCT_UNIQ
    [StateTable_minimal.xlsx]
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2020-01-06 move all EEPROM and config choice code to doPattern; regularize some code
    [StateTable_minimal.xlsx]
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2020-01-10 new unified configuration approach. Need to store state table into program space
    [StateTable_minimal.xlsx]
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2020-01-11 add the 2save variables and some new config sounds
    [StateTable_minimal.xlsx]
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2020-01-11 this version used for demo video for Jim
    [StateTable_minimal.xlsx]
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2020-01-16 get ready to add LingoJam.com robotic voice for power-on
    [StateTable_minimal.xlsx]
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2020-01-18 I think it now uses red button OK
    [RubberBandGun.sch, StateTable_minimal.xlsx]
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2020-01-20 lots of mods to get configuration of LED patterns working right. Still more to do
    [StateTable_minimal.xlsx]
2020-01-21 think the LED pattern configuration is working now
    [StateTable_minimal.xlsx]
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2020-01-25 partial implementation for copy/reset and advanced menus
    [StateTable_minimal.xlsx]
2020-01-25 add factory reset routine
    [StateTable_minimal.xlsx]
2020-01-25 add calls to factory reset routine
    [StateTable_minimal.xlsx]
2020-01-26 add intro and accept to factory reset / config copy
    [StateTable_minimal.xlsx]
2020-01-26 fix some bugs in factory reset
    [StateTable_minimal.xlsx]
2020-01-27 fixed some more bugs; ready to do configuration copies
    [StateTable_minimal.xlsx]
2020-01-27 pretty much working; funny short windup on saved config 1
    [StateTable_minimal.xlsx]
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2020-01-28 schematic update - add transistor for output, remove 2nd Arduino
    [RubberBandGun.sch]
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2020-02-01 update to KiCad 5.1.5 and implement RAM copy of EEPROM settings
    [RubberBandGun.sch, RubberBandWiring.sch, StateTable_minimal.xlsx]
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2020-02-09 fix another bug
    [StateTable_minimal.xlsx]
2020-02-09 get rid of some spurious error messages and add some better checks
    [StateTable_minimal.xlsx]
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2020-02-14 for some reason Cassini Saturn sounds don't play on YX5200
    [RubberBandGun.sch, StateTable_minimal.xlsx]
2020-02-14 needed to resample Cassini Saturn sounds to standard bit rate
    [StateTable_minimal.xlsx]
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2020-03-02 wiring for solenoid & move to pin 8
    [RubberBandGun.sch]
2020-03-14 start getting ready for 'firing too fast' message
    [StateTable_minimal.xlsx]
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2020-03-28 add Jim's Autocad Fusion 360 model of handle
    [RBG body 4.f3d, RBG body 4.stl]
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2020-07-14 update schematic to show power and USB details
    [RubberBandGun.sch, SOL.sch]
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2020-08-21 add BlueTooth Audio Tx and WS2812b Single LED for inside handle compartment
    [LEDrings.sch, RubberBandGun.sch, Solenoid.sch]
2020-08-26 correct YX5200 SPK2 wiring
    [LEDrings.sch, RubberBandGun.sch, Solenoid.sch]
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2020-09-07 add Programming Arduino for temp connection to program KCX_BT_EMITTER
    [LEDrings.sch, RubberBandGun.sch, Solenoid.sch]
2020-09-07 separating analog ground from digital ground solved the bluetooth hum problem
    [RubberBandGun.sch]
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2020-09-12 correct comment about wire color
    [ProgrammingArduino.ino]
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2020-09-20 adjust (finally) to swap of Red and Green config buttons
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2020-09-25 finish the switch between red and green buttons
    [StateTable_minimal.xlsx]
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2020-09-27 add La Cucaracha and tone down Doom sound
    [StateTable_minimal.xlsx]
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2020-10-03 struggling for correct place for LED patterns info
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2021-07-31 switch to 'demo' mode as default, static mode can be set
    [StateTable_minimal.xlsx]
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2021-09-18 add info on bitrate from the audio files; correct 004
    [StateTable_minimal.xlsx]
2021-09-18 more info on WAV files and what works with YX5200
    [StateTable_minimal.xlsx]
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2022-01-07 correct comment regarding sound attributions
    [RBG_SciFi.ino]
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2022-04-11 add motor circuit for SIDEWINDER on sheet for solenoid for SILVER
    [LEDrings.sch, ProgArd.sch, RubberBandGun.sch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]
2022-04-11 FIXME to add info on SIDEWINDER motor driver parts
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2022-05-08 no longer 'close to prototype'
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

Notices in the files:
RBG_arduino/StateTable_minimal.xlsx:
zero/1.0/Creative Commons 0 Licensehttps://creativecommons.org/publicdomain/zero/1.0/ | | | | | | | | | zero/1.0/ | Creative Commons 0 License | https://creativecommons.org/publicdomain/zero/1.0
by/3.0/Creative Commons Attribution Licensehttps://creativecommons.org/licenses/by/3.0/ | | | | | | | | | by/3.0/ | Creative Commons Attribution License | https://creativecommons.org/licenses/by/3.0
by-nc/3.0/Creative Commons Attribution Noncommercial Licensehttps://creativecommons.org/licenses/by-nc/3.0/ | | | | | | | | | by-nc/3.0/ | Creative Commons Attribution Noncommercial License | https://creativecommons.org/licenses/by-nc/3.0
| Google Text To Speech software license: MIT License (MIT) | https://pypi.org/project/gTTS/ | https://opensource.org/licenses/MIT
